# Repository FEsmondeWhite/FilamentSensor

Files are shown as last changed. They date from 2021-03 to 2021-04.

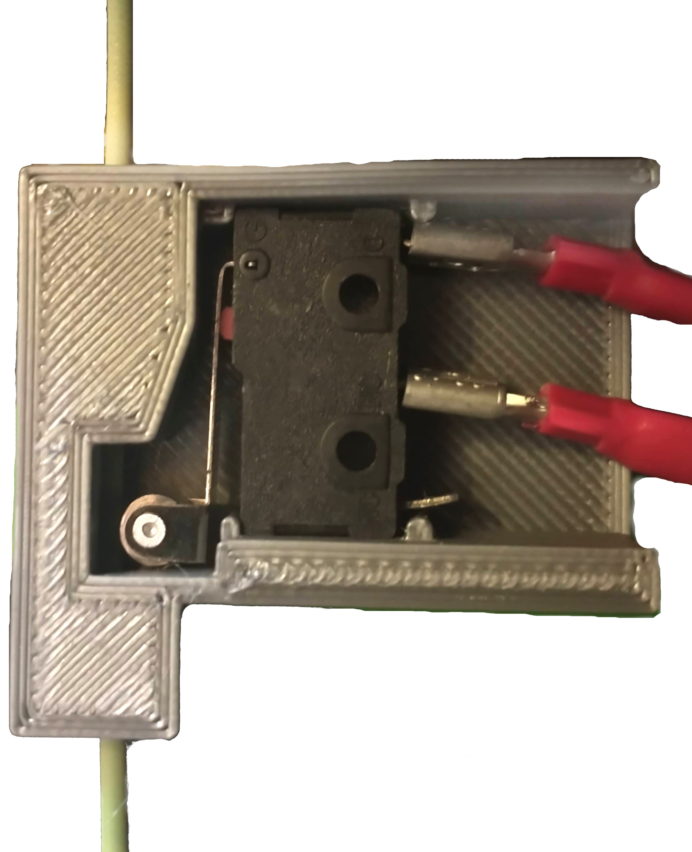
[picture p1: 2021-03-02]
FilamentRunoutSensorLighter.jpg

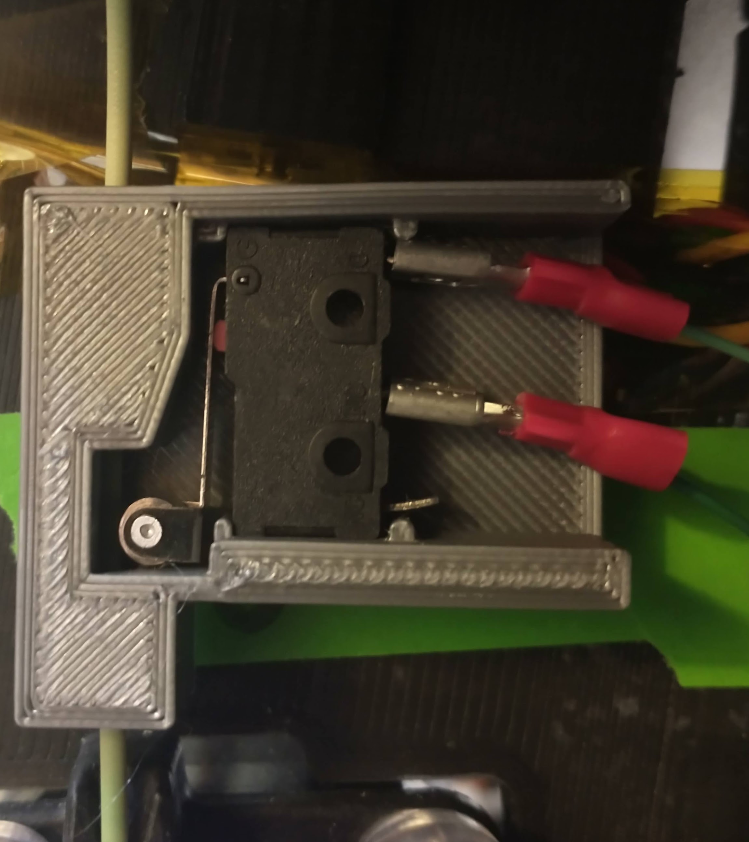
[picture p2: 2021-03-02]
FilamentRunoutSensor.jpg

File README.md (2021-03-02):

# Filament Runout Sensor
Simple roller switch based filament runout sensor. Used with Rostock Max v2 (upgraded to v3) with dual extruders.

# Description
The original mechanical housing and switch selection were sent to me as an STL file by email, I'm not sure who originally created this model (sorry for lack of attribution!). It is similar to [this one](https://www.thingiverse.com/thing:1134134). I modified the STL in Fusion 360 to improve printability (square profile prints better than round) and switch fit (including open back-end for easy connection). I have also added a wiring diagram for using this switch with the RAMBo 1.3L that is in my SeeMeCNC Rostock Max printer. I used [5A 125 250V SPDT 3 pin momentary hinge metal roller lever microswitches](https://www.amazon.com/gp/product/B07BL33XXT) to add the filament sensors.

I also modified a Teensy project to [adapt the HE280 end effector platform](https://github.com/FEsmondeWhite/HE280AccelerometerInterface) for use with the latest Repetier branch.

[Find more discussion of my Rostock Max setup on the Repetier forum](https://forum.repetier.com/discussion/8324/rostock-max-he280-accelerometer-z-probe-filament-runout-sensors).

# Assembly
One housing and switch are needed for each filament runout sensor. 3D print a housing, and press a switch into the housing, so that the roller ends up in the filament path. I used crimp-on automotive blade-style connectors to connect onto the switch, with tiny wires salvaged from an ethernet cable and dupont connectors to connect to the RAMBo board.

Switch pins 1 and 3 are connected to the RAMBo. I have connected filament sensor 1 to the X-min endstop port on the RAMBo, for use with extruder 0. Filament sensor 2 is connected to the Y-mnin endstop port on the RAMBo. The wires are connected to the ground and sensor pins, and the input is set with a pull-up in Repetier firmware. My Repetier 1.0.5 Configuration.h file is included for reference.

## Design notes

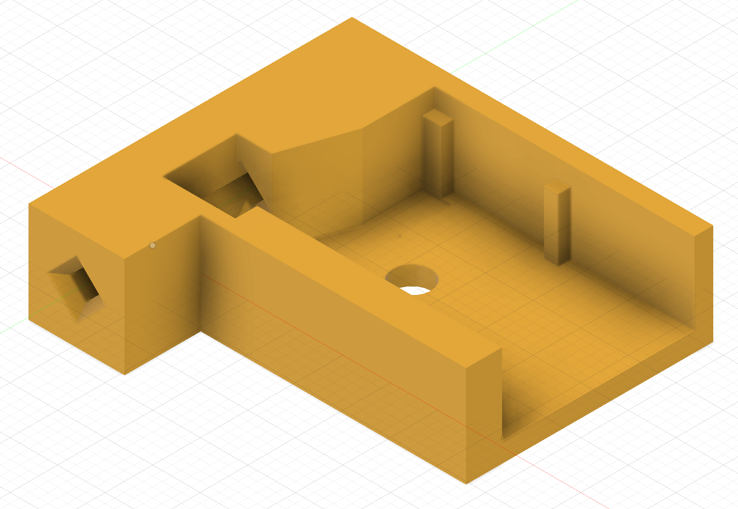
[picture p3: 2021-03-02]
mechanical/FilamentRunoutSensorHousing.png

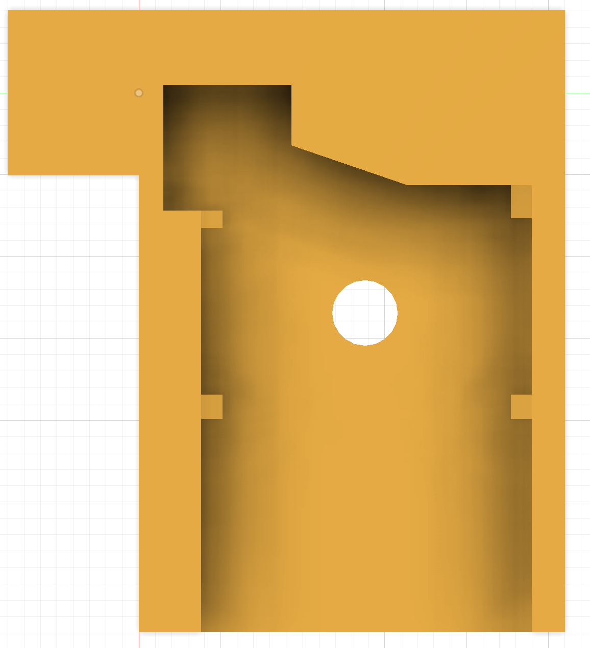
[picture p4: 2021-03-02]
mechanical/FilamentRunoutSensorHousingTop.png

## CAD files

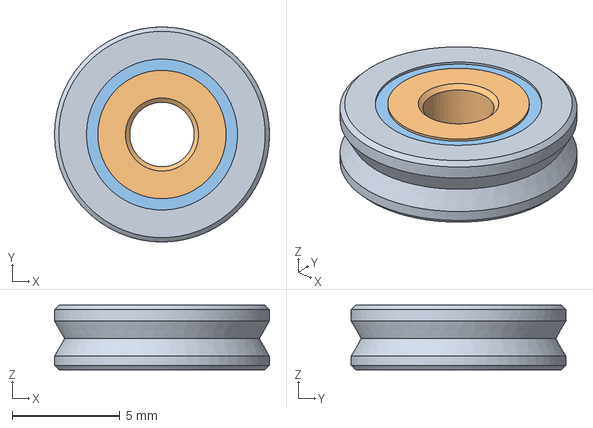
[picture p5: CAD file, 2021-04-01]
mechanical/V623-V-GrooveBearing.step
10.0 x 10.0 x 3.00 mm

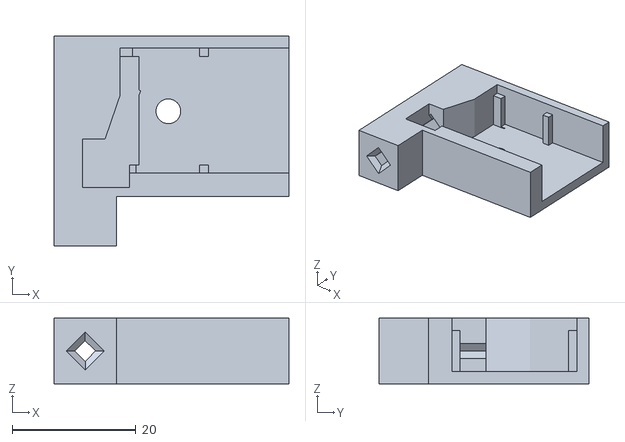
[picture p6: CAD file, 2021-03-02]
mechanical/FilamentRunoutSensorHousing.stl
38.0 x 34.0 x 10.6

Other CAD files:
mechanical/FilamentRunoutSensorHousing.f3d

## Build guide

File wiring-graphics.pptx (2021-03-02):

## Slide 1

Filament Sensor 1

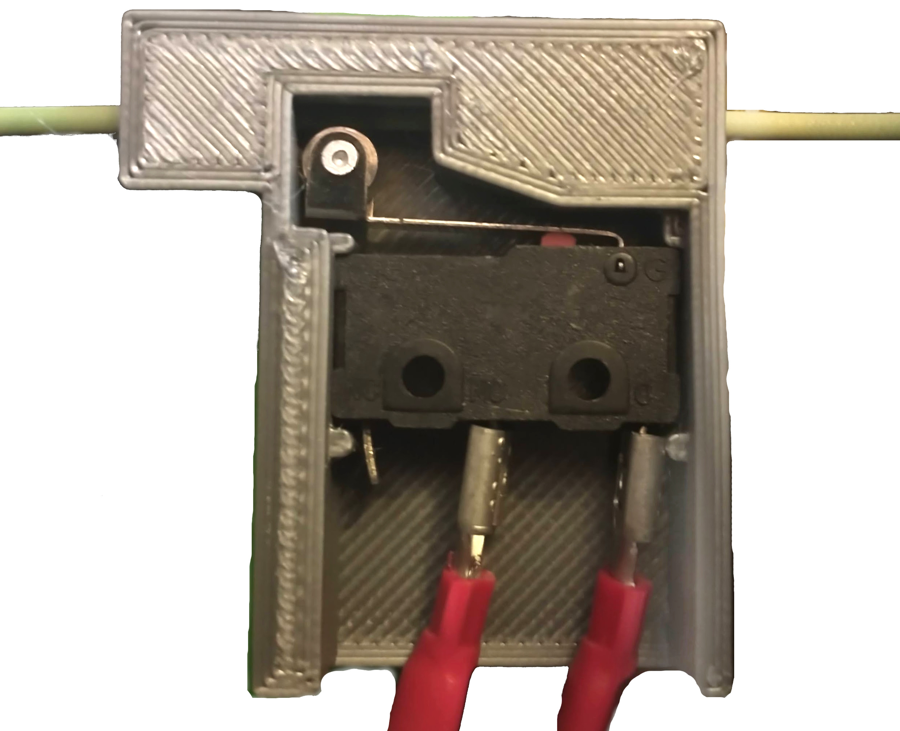
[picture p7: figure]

Filament Sensor 2

Filament direction to extruder

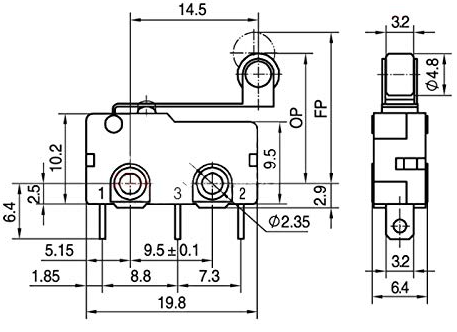
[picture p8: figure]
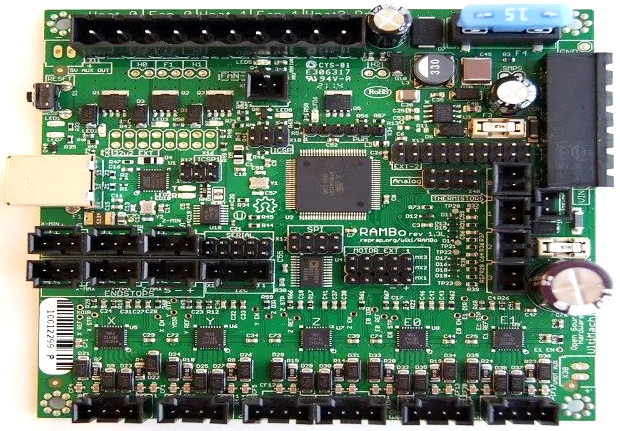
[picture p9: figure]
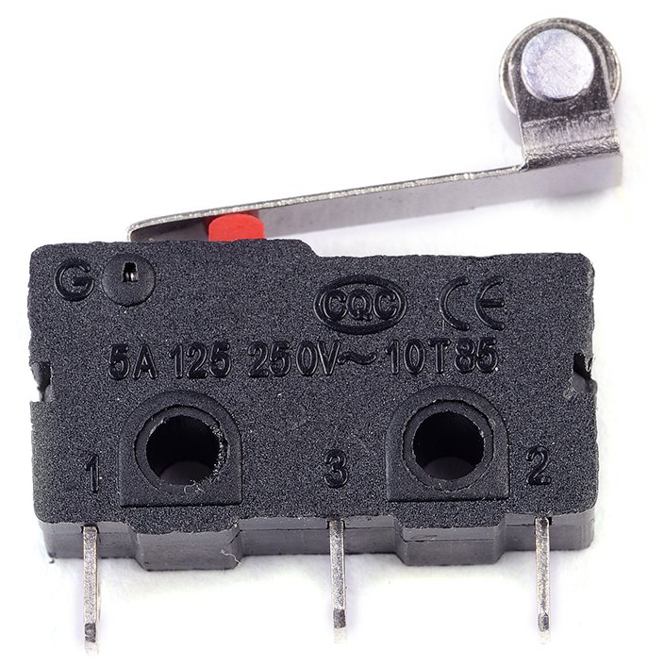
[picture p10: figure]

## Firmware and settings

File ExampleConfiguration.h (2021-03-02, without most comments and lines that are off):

#define CONFIGURATION_H
#define NUM_EXTRUDER 2
#define MOTHERBOARD 301
#include "pins.h"
#define MICROSTEP_MODES { 8,8,8,8,8 } // [1,2,4,8,16]
#define MOTOR_CURRENT_PERCENT { 55,55,55,55,55 }
#define HOST_RESCUE 1
#undef FAN_PIN
#define FAN_PIN ORIG_FAN2_PIN
#undef FAN_BOARD_PIN
#define FAN_BOARD_PIN -1
#define BOARD_FAN_SPEED 255
#define BOARD_FAN_MIN_SPEED 0
#define FAN_THERMO_PIN ORIG_FAN2_PIN
#define FAN_THERMO_MIN_PWM 128
#define FAN_THERMO_MAX_PWM 255
#define FAN_THERMO_MIN_TEMP 40
#define FAN_THERMO_MAX_TEMP 60
#define FAN_THERMO_THERMISTOR_PIN TEMP_0_PIN
#define FAN_THERMO_THERMISTOR_TYPE 8
#undef X_MIN_PIN
#define X_MIN_PIN -1
#undef Y_MIN_PIN
#define Y_MIN_PIN -1
#undef Z_MIN_PIN
#define Z_MIN_PIN -1
#define BLUETOOTH_SERIAL  -1
#define BLUETOOTH_BAUD  115200
#define MIXING_EXTRUDER 0
#define DRIVE_SYSTEM 3
#define XAXIS_STEPS_PER_MM 80
#define YAXIS_STEPS_PER_MM 80
#define ZAXIS_STEPS_PER_MM 80
#define EXTRUDER_FAN_COOL_TEMP 50
#define PDM_FOR_EXTRUDER 0
#define PDM_FOR_COOLER 0
#define DECOUPLING_TEST_MAX_HOLD_VARIANCE 20
#define DECOUPLING_TEST_MIN_TEMP_RISE 1
#define KILL_IF_SENSOR_DEFECT 0
#define RETRACT_ON_PAUSE 2
#define PAUSE_START_COMMANDS ""
#define PAUSE_END_COMMANDS ""
#define SHARED_EXTRUDER_HEATER 1
#define EXT0_X_OFFSET 0
#define EXT0_Y_OFFSET 0
#define EXT0_Z_OFFSET 0
#define EXT0_STEPS_PER_MM 80.00
#define EXT0_TEMPSENSOR_TYPE 8
#define EXT0_TEMPSENSOR_PIN TEMP_0_PIN
#define EXT0_HEATER_PIN HEATER_0_PIN
#define EXT0_STEP_PIN ORIG_E0_STEP_PIN
#define EXT0_DIR_PIN ORIG_E0_DIR_PIN
#define EXT0_INVERSE 1
#define EXT0_ENABLE_PIN ORIG_E0_ENABLE_PIN
#define EXT0_ENABLE_ON 0
#define EXT0_MIRROR_STEPPER 0
#define EXT0_STEP2_PIN ORIG_E0_STEP_PIN
#define EXT0_DIR2_PIN ORIG_E0_DIR_PIN
#define EXT0_INVERSE2 0
#define EXT0_ENABLE2_PIN ORIG_E0_ENABLE_PIN
#define EXT0_MAX_FEEDRATE 50
#define EXT0_MAX_START_FEEDRATE 20
#define EXT0_MAX_ACCELERATION 5000
#define EXT0_HEAT_MANAGER 1
#define EXT0_PREHEAT_TEMP 215
#define EXT0_WATCHPERIOD 1
#define EXT0_PID_INTEGRAL_DRIVE_MAX 230
#define EXT0_PID_INTEGRAL_DRIVE_MIN 80
#define EXT0_PID_PGAIN_OR_DEAD_TIME 20.0045
#define EXT0_PID_I 2.4816
#define EXT0_PID_D 40.3140
#define EXT0_PID_MAX 255
#define EXT0_ADVANCE_K 0
#define EXT0_ADVANCE_L 0
#define EXT0_ADVANCE_BACKLASH_STEPS 0
#define EXT0_WAIT_RETRACT_TEMP 150
#define EXT0_WAIT_RETRACT_UNITS 0
#define EXT0_SELECT_COMMANDS ""
#define EXT0_DESELECT_COMMANDS ""
#define EXT0_EXTRUDER_COOLER_PIN ORIG_FAN_PIN
#define EXT0_EXTRUDER_COOLER_SPEED 255
#define EXT0_DECOUPLE_TEST_PERIOD 12000
#define EXT0_JAM_PIN ORIG_X_MIN_PIN
#define EXT0_JAM_PULLUP 1
#define EXT1_X_OFFSET 0
#define EXT1_Y_OFFSET 0
#define EXT1_Z_OFFSET 0
#define EXT1_STEPS_PER_MM 80.000
#define EXT1_TEMPSENSOR_TYPE 8
#define EXT1_TEMPSENSOR_PIN TEMP_0_PIN
#define EXT1_HEATER_PIN HEATER_0_PIN
#define EXT1_STEP_PIN ORIG_E1_STEP_PIN
#define EXT1_DIR_PIN ORIG_E1_DIR_PIN
#define EXT1_INVERSE 1
#define EXT1_ENABLE_PIN ORIG_E1_ENABLE_PIN
#define EXT1_ENABLE_ON 0
#define EXT1_MIRROR_STEPPER 0
#define EXT1_STEP2_PIN ORIG_E1_STEP_PIN
#define EXT1_DIR2_PIN ORIG_E1_DIR_PIN
#define EXT1_INVERSE2 0
#define EXT1_ENABLE2_PIN ORIG_E1_ENABLE_PIN
#define EXT1_MAX_FEEDRATE 50
#define EXT1_MAX_START_FEEDRATE 20
#define EXT1_MAX_ACCELERATION 5000
#define EXT1_HEAT_MANAGER 1
#define EXT1_PREHEAT_TEMP 190
#define EXT1_WATCHPERIOD 1
#define EXT1_PID_INTEGRAL_DRIVE_MAX 230
#define EXT1_PID_INTEGRAL_DRIVE_MIN 40
#define EXT1_PID_PGAIN_OR_DEAD_TIME 7
#define EXT1_PID_I 2
#define EXT1_PID_D 40
#define EXT1_PID_MAX 255
#define EXT1_ADVANCE_K 0
#define EXT1_ADVANCE_L 0
#define EXT1_ADVANCE_BACKLASH_STEPS 0
#define EXT1_WAIT_RETRACT_TEMP 150
#define EXT1_WAIT_RETRACT_UNITS 0
#define EXT1_SELECT_COMMANDS ""
#define EXT1_DESELECT_COMMANDS ""
#define EXT1_EXTRUDER_COOLER_PIN -1
#define EXT1_EXTRUDER_COOLER_SPEED 255
#define EXT1_DECOUPLE_TEST_PERIOD 12000
#define EXT1_JAM_PIN ORIG_Y_MIN_PIN
#define EXT1_JAM_PULLUP 1
#define FEATURE_RETRACTION 1
#define AUTORETRACT_ENABLED 0
#define RETRACTION_LENGTH 3
#define RETRACTION_LONG_LENGTH 13
#define RETRACTION_SPEED 20
#define RETRACTION_Z_LIFT 0
#define RETRACTION_UNDO_EXTRA_LENGTH 0
#define RETRACTION_UNDO_EXTRA_LONG_LENGTH 0
#define RETRACTION_UNDO_SPEED 10
#define FILAMENTCHANGE_X_POS 0
#define FILAMENTCHANGE_Y_POS 0
#define FILAMENTCHANGE_Z_ADD  20
#define FILAMENTCHANGE_REHOME 2
#define FILAMENTCHANGE_SHORTRETRACT 5
#define FILAMENTCHANGE_LONGRETRACT 100
#define JAM_METHOD 3
#define JAM_STEPS 220
#define JAM_SLOWDOWN_STEPS 320
#define JAM_SLOWDOWN_TO 70
#define JAM_ERROR_STEPS 500
#define JAM_MIN_STEPS 10
#define JAM_ACTION 1
#define RETRACT_DURING_HEATUP true
#define PID_CONTROL_RANGE 20
#define SKIP_M109_IF_WITHIN 2
#define SCALE_PID_TO_MAX 0
#define TEMP_HYSTERESIS 5
#define EXTRUDE_MAXLENGTH 160
#define NUM_TEMPS_USERTHERMISTOR0 0
#define USER_THERMISTORTABLE0 {}
#define NUM_TEMPS_USERTHERMISTOR1 0
#define USER_THERMISTORTABLE1 {}
#define NUM_TEMPS_USERTHERMISTOR2 0
#define USER_THERMISTORTABLE2 {}
#define GENERIC_THERM_VREF 5
#define GENERIC_THERM_NUM_ENTRIES 33
#define TEMP_GAIN 0
#define HEATER_PWM_SPEED 0
#define COOLER_PWM_SPEED 2
#define HAVE_HEATED_BED 1
#define HEATED_BED_PREHEAT_TEMP 55
#define HEATED_BED_MAX_TEMP 120
#define SKIP_M190_IF_WITHIN 5
#define HEATED_BED_SENSOR_TYPE 8
#define HEATED_BED_SENSOR_PIN 2
#define HEATED_BED_HEATER_PIN 3
#define HEATED_BED_SET_INTERVAL 5000
#define HEATED_BED_HEAT_MANAGER 1
#define HEATED_BED_PID_INTEGRAL_DRIVE_MAX 255
#define HEATED_BED_PID_INTEGRAL_DRIVE_MIN 80
#define HEATED_BED_PID_PGAIN_OR_DEAD_TIME   43.837
#define HEATED_BED_PID_IGAIN   1.027
#define HEATED_BED_PID_DGAIN 467.926
#define HEATED_BED_PID_MAX 255
#define HEATED_BED_DECOUPLE_TEST_PERIOD 300000
#define MIN_EXTRUDER_TEMP 150
#define MAXTEMP 270
#define MIN_DEFECT_TEMPERATURE -10
#define MAX_DEFECT_TEMPERATURE 290
#define MILLISECONDS_PREHEAT_TIME 30000
#define SUPPORT_LASER 0
#define LASER_PIN -1
#define LASER_ON_HIGH 1
#define LASER_WARMUP_TIME 0
#define LASER_PWM_MAX 255
#define LASER_WATT 2
#define SUPPORT_CNC 0
#define CNC_WAIT_ON_ENABLE 300
#define CNC_WAIT_ON_DISABLE 0
#define CNC_ENABLE_PIN -1
#define CNC_ENABLE_WITH 1
#define CNC_DIRECTION_PIN -1
#define CNC_DIRECTION_CW 1
#define CNC_PWM_MAX 255
#define CNC_RPM_MAX 8000
#define CNC_SAFE_Z 150
#define DEFAULT_PRINTER_MODE 0
#define MULTI_ZENDSTOP_HOMING 0
#define ENDSTOP_PULLUP_X_MIN true
#define ENDSTOP_X_MIN_INVERTING false
#define MIN_HARDWARE_ENDSTOP_X false
#define ENDSTOP_PULLUP_Y_MIN true
#define ENDSTOP_Y_MIN_INVERTING false
#define MIN_HARDWARE_ENDSTOP_Y false
#define ENDSTOP_PULLUP_Z_MIN false
#define ENDSTOP_Z_MIN_INVERTING false
#define MIN_HARDWARE_ENDSTOP_Z false
#define ENDSTOP_PULLUP_Z2_MINMAX true
#define ENDSTOP_Z2_MINMAX_INVERTING false
#define MINMAX_HARDWARE_ENDSTOP_Z2 false
#define ENDSTOP_PULLUP_X_MAX true
#define ENDSTOP_X_MAX_INVERTING false
#define MAX_HARDWARE_ENDSTOP_X true
#define ENDSTOP_PULLUP_Y_MAX true
#define ENDSTOP_Y_MAX_INVERTING false
#define MAX_HARDWARE_ENDSTOP_Y true
#define ENDSTOP_PULLUP_Z_MAX true
#define ENDSTOP_Z_MAX_INVERTING false
#define MAX_HARDWARE_ENDSTOP_Z true
#define ENDSTOP_PULLUP_X2_MIN true
#define ENDSTOP_PULLUP_Y2_MIN true
#define ENDSTOP_PULLUP_Z2_MINMAX true
#define ENDSTOP_PULLUP_X2_MAX true
#define ENDSTOP_PULLUP_Y2_MAX true
#define ENDSTOP_X2_MIN_INVERTING false
#define ENDSTOP_Y2_MIN_INVERTING false
#define ENDSTOP_X2_MAX_INVERTING false
#define ENDSTOP_Y2_MAX_INVERTING false
#define MIN_HARDWARE_ENDSTOP_X2 false
#define MIN_HARDWARE_ENDSTOP_Y2 false
#define MAX_HARDWARE_ENDSTOP_X2 false
#define MAX_HARDWARE_ENDSTOP_Y2 false
#define X2_MIN_PIN -1
#define X2_MAX_PIN -1
#define Y2_MIN_PIN -1
#define Y2_MAX_PIN -1
#define Z2_MINMAX_PIN -1
#define max_software_endstop_r true
#define min_software_endstop_x true
#define min_software_endstop_y true
#define min_software_endstop_z true
#define max_software_endstop_x false
#define max_software_endstop_y false
#define max_software_endstop_z false
#define DOOR_PIN -1
#define DOOR_PULLUP 1
#define DOOR_INVERTING 0
#define ENDSTOP_X_BACK_MOVE 5
#define ENDSTOP_Y_BACK_MOVE 5
#define ENDSTOP_Z_BACK_MOVE 5
#define ENDSTOP_X_RETEST_REDUCTION_FACTOR 3
#define ENDSTOP_Y_RETEST_REDUCTION_FACTOR 3
#define ENDSTOP_Z_RETEST_REDUCTION_FACTOR 3
#define ENDSTOP_X_BACK_ON_HOME 5
#define ENDSTOP_Y_BACK_ON_HOME 5
#define ENDSTOP_Z_BACK_ON_HOME 5
#define ALWAYS_CHECK_ENDSTOPS 1
#define MOVE_X_WHEN_HOMED 0
#define MOVE_Y_WHEN_HOMED 0
#define MOVE_Z_WHEN_HOMED 0
#define X_ENABLE_ON 0
#define Y_ENABLE_ON 0
#define Z_ENABLE_ON 0
#define DISABLE_X 0
#define DISABLE_Y 0
#define DISABLE_Z 0
#define DISABLE_E 1
#define INVERT_X_DIR 1
#define INVERT_X2_DIR 0
#define INVERT_Y_DIR 0
#define INVERT_Y2_DIR 0
#define INVERT_Z_DIR 1
#define INVERT_Z2_DIR 0
#define INVERT_Z3_DIR 0
#define INVERT_Z4_DIR 0
#define X_HOME_DIR -1
#define Y_HOME_DIR -1
#define Z_HOME_DIR 1
#define X_MAX_LENGTH 200
#define Y_MAX_LENGTH 200
#define Z_MAX_LENGTH 366.763
#define X_MIN_POS 0
#define Y_MIN_POS 0
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

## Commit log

2021-03-02 Simple filament runout sensor
    Example filament runout sensors for Rostock Max V2/V3 and the RAMBo 1.3L board with configuration for Repetier 1.0.5.
    [FilamentRunoutSensorHousing.f3d, FilamentRunoutSensorHousing.stl]
2021-04-01 Added v-groove bearing file.
    [V623-V-GrooveBearing.step]

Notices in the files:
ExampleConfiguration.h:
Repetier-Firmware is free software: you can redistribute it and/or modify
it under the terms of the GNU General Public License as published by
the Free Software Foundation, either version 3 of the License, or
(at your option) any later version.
